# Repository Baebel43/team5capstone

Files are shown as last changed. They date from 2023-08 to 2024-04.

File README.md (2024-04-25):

# Ride Replay System 

## Executive Summary

Currently, there are no commercially available devices that officially allow people to ride a personal recording of a trail, Team 5 aims to change this with the Ride Replay Kit. The Ride Replay Kit aims to offer users the ability to replay a trail recorded anywhere with the same difficulty and immersion as if the rider was actually on that trail.

## Capabilities

The Project is able to do the following. For the indoor exercise bike, it is able to take a video and replay it on the trail with the ability to scale the video up and down based on the speed of the user. The Fan attached to the front of the indoor exercise bike will also scale with the user's speed. The outdoor bike that will have the ride replay kit attached is able to take in elevation data in after every full rotation of the back wheel. The full rotations are taken when the magnet attached to the spoke passes by the hall effect sensor attached to the back of the bike. This data is then saved to a text file and it can then be turned into a byte array for use inside the linear actuator code. The outdoor bike also has the ability to record audio from the microphone and store it on the Raspberry Pi. The Arduino IOT devices have the ability to communicate the weight input from the load cells and send them to the main controller Arduino IOT, these will be label so that future teams can know which is the slave and which is the master.

## Salient Outcomes

Being able to run the User Interface, the code to scale the video, the fan scale code, and the tachometer at the same time. Additionally the ability to use previous teams raspberry pi to record audio and a workmap accurately.

## Project Demonstration & Images

Minimally Functional Prototype link - https://youtu.be/p_Y5p9GWvbA

Ride Replay Kit - https://youtube.com/watch?v=LAPSdsN-WzQ&feature=shared

Final Trail Recording - https://www.youtube.com/shorts/GgyuamzpSRI

Exercise Bike Test - https://www.youtube.com/shorts/0spRPyzmJK8

## About Us

### Team 5
Team 5 is a six-person Fall 2023 to Spring 2024 Capstone Design team comprised of 5 Electrical Engineers and 1 Computer Engineers. The Team includes: Utsav Singa, Caleb Rozenboom, Jayden Marcom, Jesse Brewster, Caleb Turney, and Benjamin Ebel

#### Utsav Sigha
* Electrical Engineering Major
* Video System
* Video Software/Hardware

#### Caleb Rozenboom
* Electrical Engineering Major
* Resistance System
* Hardware

#### Jayden Marcom
* Electrical Engineering Major
* Work System
* Hardware

#### Jesse Brewster
* Electrical Engineering Major
* Audio System
* Audio Software/Hardware

#### Caleb Turney
* Electrical Engineering Major
* Immersion System
* Immersion Software and Hardware

#### Ben Ebel
* Computer Engineering Major
* GUI System
* Software/Coding in Python and C

### Faculty Supervisor

Professor Jesse Roberts of the Electrical and Computer Engineering Department of Tennessee Technological University.

### Stakeholders

The consumers of this project are mountain biking enthusiasts, exercise bicycle enthusiasts, and any person interested in an escape to a faraway place without the time or finances to do so. 

### Recognitions
* Jesse Roberts
* Conard Murray
* Jeff Randolph 
* Jeffrey Austen
* Sterling Sloan

## Repo Organization

This GitHub is comprised of 3 main files: Documentation, Reports, and Software.

### Reports

In the reports section of this repository information about the individual expectations for the reports and how they should be housed is provided.

### Documentation

In the documentation section information regarding the documentation that is required and how it should be organized is given.

### Software

In the software directory of the repo information regarding how each team is expected to document software can be found.

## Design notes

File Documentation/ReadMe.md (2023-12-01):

## Documentation Folder

This folder contains the folders for the signoffs, 3D models, Wiring Schematics, images, signoffs, and images for all of the subsystems

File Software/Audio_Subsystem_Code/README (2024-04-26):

This is the audio subsystem python code.

The Recording_microphone.py code is used to record the audio from the bike trail on the trail bike.
This code operates on the Raspberry Pi 3 within the Ride Replay kit. 
Run the code using a keyboard or SSH in to the Raspberry Pi.
The code will instantly start recording the audio from the microphone attached to the front of the bike. 
Then once the user has completed the trail. Jumper two pins 35 and 37 of the Raspberry Pi together and this will stop the recording. Alternatively, press "Enter" on the keyboard to stop.

The Audio_sectionalizing.py code is operated off of a separate computer. 
Place the name of the recorded trail audio file within the code and run.
An example code of the recorded trail audio file is "recorded_audio_2024-04-25_20-02-52.wav". Input this as the 'input_audio_file' varible on line 41 of the code.
This code divides the trail audio into 30 second sections, not matter the length of the video. The total number of audio files are outputted in the terminal. The audio files that are generated are label as "sectioned_audio_n" where 'n' is the number of the sectionalized audio file. 

The Playback.py code can be found on the Raspberry Pi 3 within the exercise bike. This code can be called within the main code 'RideReplayKitMainCode.py' where it runs. The 30-second sections of audio will play back based upon the feedback from the resistance system, where they will loop until the user has progressed to the next audio section. This syncs the audio with the user biking on the exercise bike.

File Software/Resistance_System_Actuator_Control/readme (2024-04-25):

This folder contains all the necessary code to run the linear actuator on the raspberry pi.

Once the workmap has been uploaded in a text file (WorkMapTest.txt), ActuatorControl.py pulls the file into an array which then is iterated through the equation in the Signoff.
To send the distance of the actuator (mm) to the actuator, it must be scaled by 0.1068 (Approximately. This value needs further calibration by testing each value with the actual distance.).

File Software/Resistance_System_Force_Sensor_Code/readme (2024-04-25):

This folder contains all code needed to allow the load cells to detect weight. 

Here is the link to the Amazon product where many helpful comments on setting up can be found:
https://www.amazon.com/DIYmalls-Weight-Digital-Amplifier-Arduino/dp/B09W2K13ZY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

For the HX711 board, here is the link for example code:
https://learn.sparkfun.com/tutorials/load-cell-amplifier-hx711-breakout-hookup-guide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

The Master.ino and Slave.ino code is for BLE transmission of the weight values (in lbs) from an Arduino IOT (slave) on the pedals and an Arduino IOT (master) which connects to the raspberry pi.

Helpful hints:
Make sure there is space below the load cells for the middle to bend. 
Keep the same calibration factor

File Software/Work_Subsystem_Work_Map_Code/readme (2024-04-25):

To set up the Work Map creation code you can find it in /scripts/testing/new as Work_Subsystem.py on the ride replay kit raspberry pi. You will need to power the Raspberry pi using a battery and start it either using an ssh or a hdmi plus keyboard. When you are finished jump the 35th pin to the 33rd pin and a workmap.txt will be created. The code will take pressure measurements every pass of the backwheel and will create an array using these values. These values can then be passed to the resistance subsystems code to be converted to height then to potential energy then to a workmap to be used by the resistance subsystem.

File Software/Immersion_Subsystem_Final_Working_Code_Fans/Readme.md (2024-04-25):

This is the code for the Atmega 2560 that is used to control the Fans.

This code controls both the PWM that drives the fan and the I2C connection the Raspberry Pi that allows that the Pi and Arduino to send data to each other. Make sure to consult the wiring schematic to ensure all the wires are connected to the correct ports or the code will not run properly. 

Also note that this code was created to run on the Arduino Atmega 2560. If you wish to run the code on a different Arduino, some of the registers and commands will need to be changed accordingly to match.

## Steps to Run Code:

1: Ensure that proper wiring has been done for the Arduino and Raspberry pi via the schematic. Ensure that the grounds of the external DC supply, Arduino, and Raspberry Pi are all connected. Ensure that the SCL and SDA pins on the Rpi are connected to the SCL and SDA pins on the Atmega. Ensure that the PWM wire of the fan is connected to Pin 9 on the Atmega.

2: Make sure that both the Arduino code and Raspberry Pi code are running simultaneously else there will be no connection and no data will be sent. Consult the Raspberry Pi software documentation for the necessary code to run.

3: Ensure that the power switch is set to on for the Immersion system enclosure, and that the fans are toggled on in the GUI. Failure to do so will result in the fans not running properly.

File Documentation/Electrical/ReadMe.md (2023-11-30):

This folder contains KiCad source files and PDFs for each of the subsystems.

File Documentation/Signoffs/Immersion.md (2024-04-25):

Team 5 - Ride Replay Kit

Team Members: Benjamin Ebel, Jayden Marcom, Jesse Brewster, Caleb Rozenboom, Utsav Singha, Caleb Turney

# Detail Design: Immersion System

##  Subsystem Functionality

The immersion subsystem will drive fans that are pointed toward the user. A tachometer on the bike wil be used to indicate how fast the user is virtually moving. Based on the speed measured, the fans will rotate at a specific RPM. The faster the measured speed, the faster the fans will rotate. The goal will be for the fans to simulate the speed of the wind outside by outputting at the same or scaled but similar wind speed. By having the fans adapt and change their speed based on the riders speed, a more immersive experience can be achieved, since the user will be able to artificially feel the changes in their speed.

Components from previous iterations of this project will be utilized for this subsystem. A tachometer was added to the bike by a previous team that was used as a speed sensor for the ride replay system. The previous speed sensor would take data from the bike as the user rode the trails, then that data would be sent through ble to a raspberry pi. The fans will be connected to this raspberry pi and the speed sensor data will used to either increase or decrease the rpm of the fans. Previous codes for the microcontroller will be utlized to allow ble communication and new code will be added to properly connect the fans to speed that is read. The previous power distribution system will also be used to power the fans. 

## Constraints 

|Constraint |Description |
|---|---|
|Off Switch| The Immersion system shall have an off switch implemented that allows the user to disable the system.|
|Fan Mapping| The fans will be mapped to output at a scaled version of outside wind speed |
|Fan Control| The speed of the fans will be adjustable and adaptable|
|Minimum RPM (DESCOPED)| The fan shall spin at a minimum of 1,105 RPM|
|Output Noise Level| The fans will have a max noise level output of 65 dBA|
|Power|Each of the fans will be supplied a minimum of 28.80 watts of power|

## Analysis

### Meeting the Fan Mapping Constraint

The speed from the previously installed speed sensor system will be used as the comparison data to decide on the fans speed. As the speed is read, the fans will change to rpm that is meant to simulate that speed. This Rpm will be based on many calculations that aim to match the outputted wind speed of the fans to the wind speed outside linearly.

Although the max speed one can achieve on a bike is above 100 mph, the average speed that a user will ride is anywhere between 10 for inexperienced riders up to 24 mph for more experienced riders [3]. This speed can reach upwards of 30 and 35 when the user is on an incline. With this in mind, the max wind speed of the fans will be connected to a max speed of 35 mph on the bike.

When it comes to choosing a fan for the immersion subsystem, it is important that the fan has a high enough CFM (Cubic Feet per Minute) value. CFM is the measurement of the volume of air that a fan is capable of moving. In order to convert CFM to a speed value you would have to know the measurements of the room and the static pressure within it. For the scope of this project, the goal is not to circulate air in the room but to push air from the fans on to the face of the user. It is impossible to precisely calculate the speed and the force that a fan will produce in an open space without being able to physically test it. So, for the sake of simplicity, a fan with a comparatively high CFM will be chosen and if the max power and speed ends up being too high then the maximum RPM of the fan will be limited. A PC cooling fan will have on average between 50-80 CFM depending on the quality and the size. This value needs to be marginally higher in order for the wind from the fans to reach the user and provide any sort of noticeable force. Therefore, the CFM-A225BF-158-597-22 has been chosen with a CFM value of 185.5 [2]. Extra testing will need to be done in regards to the distance of the positioning of the fans and their max power output, but this value should be adequate in pushing enough air towards the user to provide an immersive experience through changing speeds.

The goal of the immersion system is to have the speed of the wind that the fans output match the speed of wind outside while the user is traveling. Although there are many factors that can affect wind speed from a fan, for the sake of this project, it will be assumed that the air around the fan is perfectly stationary and all the air movement comes from the fans alone. It will also be assumed that the cross sectinal area that the flan is blowing into will be equal to the circumference of the fan. The diameter of entire CFM-A225BF-158-597-22 fan frame is 120mm, there is approximately 10 mm of frame so the diameter of the actual fan will be taken as 110 mm. This makes the radius equal to 55mm so if we find the cross sectional area, which is πr^2, then we get an area of 0.1023 square feet. The datasheets for fans do not include their winds speeds but instead their CFM so these values must be converted to get an idea of what the fans output wind speed will be. The formula to convert Cubic Feet per Minute to Feet per Minute is [9]:

**$$\ FPM = CFM/(Cross Sectional Area)$$**

Then by converting the Feet per minute to miles per hour, you get the wind speed in MPH.

If we take the max CFM value of the CFM-A225BF-158-597-22 fan, which is 185.5, then divide by the area of 0.1023 square feet and convert to mph, then we acquire an mph equivalent value of 20.6056 Mph. This will be used as the max value for the fan wind speed, and to connect it to the speed of the user the values will be scaled to match. This means that for the scope of this design, 20.6056 mph will be equal to 35 mph, which is the range of the outside wind speed values scaled down by 41.13%. With this scale factor in place, the cfm values for each mph in the range can be found, and then the appropriate rpm can be apllied.



Figure 1. Full Data set for MPH to RPM

As Shown in figure 1, the values from the speed range are scaled down to fit parameters, then using the CFM to MPH conversion formula that was previously outlined, the CFM at each of those scaled speed values is found. As will be explained more later, the CFM values for a fan and the RPM are directly proportional[8]. So by taking the max CFM value of 185.5 and the max RPM value of 5800 for the CFM-A225BF-158-597-22 fan, a ratio of 31.24 RPM to every CFM can be calculated. Using this, the relative RPM values for each of the calculated CFM values was found. 
For speeds of 1-6mph then value of the rpm of the fans will be set to the minimum value contraint of 1,105 rpm. This will be explained in detail further into the analysis but the purpose is to provide a minimum speed that will be required for air to reach the user.

These values match up to the desired range of wind speeds and relate to the speed of the outside wind linearly. In the code pwm code for the fans these values will be used as the basis for the speed of the fans, as the tachometer sends values the speed will be read, then the fan will change to the appropriate RPM value.

### Meeting the minimum RPM Constraint. (DESCOPED CONSTRAINT)

When calculating to rpms needed to create certain wind speeds with the fan, it is important to take into account how much air the fan will push, and if the amount of air will be sufficient when the fan runs at very low RPMS. The fans will be positioned apporiximately 1 meter away from the user, for the purpose of this project, we will assume that the minimum area that the fan will need to be able to blow air is a cubic meter. This translate to 35.3147 square feet of space. When it comes to CFM and RPM for fans, they are directly proportional[8]. This means for a 10% increase in rpm there will be an equivalent 10% increase in cfm. The max rpm of the CFM-A225BF-158-597-22 is 5800, and the max cfm is 185.5. This means that for every 1 CFM, there is an equivalent 31.266 RPM. If we take the 35.3147 Cubic feet value that was decided earlier, and translate that to an equivalent RPM value we get 35.3147 x 31.266 = 1,104.149 RPM. This is the hypothetical value based on calculations that the minimum fan speed needs to be to push air in a cubic meter of space, and this is ignoring any outside factors of static pressure or air flow. 

The minimum value that the fan will output is 1105 rpm, this will allow the user to feel the air even at the lower speeds where the calculated fan speed would initially not have been able to push enough air to reach the user. This is in line with the minimum constraint.
 
### Meeting the Fan Control Constraint

To create an immersive riding experience for the user, it is important that the fans are controllable and able to change their output based on the speed that the user is traveling. The CFM-A225BF-158-597-22 is PWM controllable meaning that it can be hooked up the PWM output of the Raspberry pi and its speed can be programmed using pulse width modulation. The speed of the user will be taken from the tachometer and sent to the Rpi and a code will be ran to use that speed data and convert it to a proportional output for the fan. As the speed data that is sent gets changed, a change in the speed of the fans will be noticeable as well. 

### Meeting Off Button Constraint

In the case that the user does not want to make use of the immersion subsystem, an off switch will be programmed into the fan code that will allow the user to shut the subsytem off. This will keep the fans from outputting until the user decides that they want to turn it back on. 

### Meeting Output Noise Level Constraint

While the OSHA standard limit for noise level is under 85 dB for 8 hours, that is not the only constraint that should be taken into account when using fans. For this susbsystem, the fans should be fast enough to properly provide air to the user, but not be so loud as to cause discomfort. Around 60 dB is the sound level of a normal conversation and past this noises start to be considered loud and potentially annoying. With this is mind, the constraint of 65 dB has been set for the fans maximum sound output. At this noise level, the fans will be very noticeable and easily heard but not at the level that should cause pain or discomfort to individuals.

According to the datasheet of the fan CFM-A225BF-158-597-22, it has a rated noise level 59.7 dBA. This value is less than 65 dBA meaning this fan will be sufficient in fulfilling this constraint.

### Meeting power constraint

<!-- In the previous renditions of this project, the groups created a power distribution system to power their componenets. The same method of powering will be used for the fans. The fans will be connected to the already installed raspberry pi which will deliver the necessary power. The raspberry pi being used is the Model 3 B+. The recommended amperage limit for the pi is 2.5 amps. The CFM-A225BF-158-597-22 is rated to operate at 5 VDC and an input current of 0.57 A. This equates to a total power draw of 2.85 Watts. The power distribution system is comprised of multiple DIN rail power supplies, each of which is capable of delivering 35 watts of power or more. Since two fans will be used for this subsystem, a total power of 6.648 W will be needed. This is within the capabilities of the previously built power system meaning the fans will be delivered their full power and be able to operate within their full range. -->

When it comes to the goal of this subsystem, it is important that the fans are powerful enough to push winds towards the user that provides ample force that is at least partially indicative of a physical trail riding experience. When considering the 5V fan options available on the market, they are not powerful enough or provide enough cfm to produce much wind force without being within a very close proximity to the user. With this in mind, 12V options had to be taken into account with the goal of a successful immersion system in mind. The Rpi is only capable of powering up to 5V fans, so an external power supply will need to be utilized in order to provide ample power to the fans and let them operate at their full range. The fans will be connected to the PWM GPIO of the raspberry pi and powered by an external source. 

The CFM-A225BF-158-597-22 fan is a 12V fan that is rated to have a current draw of 2.4 Amps equalling out to a power draw of 28.8 Watts. With there being two fans that means the total power draw will be 57.6 amps. With this in mind, a 12V 5A 60W power supply has been chosen to power the fans. It comes with a female DC connector piece that will allow a connection to fans. 

The CFM-A225BF-158-597-22 has 4 connections wires: +Vin, -Vin, and Tach signal, and PWM signal. The fan speed will be controlled via the PWM0 port GPIO12 on the raspberry pi. The fans will be connected to the external 60W power supply.

## Buildable Schematic



Figure 2. Circuit Schematic for Fan Connection to Raspberry pi

## Bill of Materials

|Item|Description|Part Number|Manufacturer|Quantity|Individual Price|Total|
|----|---|---|---|---|---|-----|
|Fan|DC Brushless Fan|CFM-A225BF-158-597-22|CUI Devices|2|$35.85|$71.7|
|PSU|DC 12V 5A 60W Power Supply||Arybroourd|1|$10.87|$10.87|
|Total|||Total Components|2|Total Cost|$82.57|

## References:

[1]“Decibels dBA,” Decibels dba, https://silentpc.com/articles/decibels (accessed Feb. 11, 2024). 

[2] “CFM-120BF series datasheet - axial fans - cui devices,” SERIES: CFM-120BF | DESCRIPTION: DC AXIAL FAN, https://www.cuidevices.com/product/resource/cfm-a225bf-153-577.pdf (accessed Feb. 12, 2024). 

[3] “Average cycling speed for new and experienced cyclists,” Road Bike, https://www.road-bike.co.uk/articles/average-speed.php (accessed Feb. 12, 2024). 

[4] T. N. Crouch, D. Burton, Z. A. LaBry, and K. B. Blair, “Riding against the wind: A review of Competition Cycling Aerodynamics - Sports Engineering,” SpringerLink, https://link.springer.com/article/10.1007/s12283-017-0234-1 (accessed Feb. 18, 2024). 

[5] J. Quinones, “4 ways to calculate wind load,” wikiHow, https://www.wikihow.com/Calculate-Wind-Load (accessed Feb. 18, 2024). 

[6] "DC 12 Volt 5 Amp Power Supply - 60W https://www.amazon.com/Supply-Adapter-100-235V-50-60Hz-Connector/dp/B0BJVVBBMJ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

[7] “Fan wind speed calculator,” Calculator Academy, https://calculator.academy/fan-wind-speed-calculator/ (accessed Feb. 22, 2024). 

[8] E. Gutowski, “The 3 fan laws and fan curve charts,” HVAC School, https://hvacrschool.com/the-3-fan-laws-and-fan-curve-charts/ (accessed Feb. 23, 2024). 

[9] M. A. Instructor, “Calculating CFM or velocity across a coil or in ductwork,” MEP Academy, https://mepacademy.com/calculating-cfm-or-velocity-across-a-coil-or-in-ductwork/# (accessed Feb. 23, 2024).

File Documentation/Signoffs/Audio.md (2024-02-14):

# Detail Design: Audio System
The audio subsystem records the audio from the bike trail and replays it on the exercise bike for the user to hear the environment of the trail.

##  Subsystem Functionality

The audio subsystem will use a unidirectional microphone mounted to the mountain bike to record audio from the trail. The audio will be recorded to a Raspberry Pi where a Python code will send it to a cloud based service where it will be processed to remove unwanted noises and improve audio quality through equalization and audio compression. The audio will also be divided into loop points depending on key points of interest throughout the trail. This processed audio will then go back on the Ride Replay Kit to the speakers of the exercise bike for playback while riding the trail. A separate Raspberry Pi will be responsible for the playback of the audio to the speakers. The audio should sync with the work map to give the user an accurate audio experience for when the user comes across different environments which produce different sounds. The speakers on the exercise bike will be mounted to the sides of the TV and allow the user to hear from both the left and right.

## Constraints 

|Constraint|Description|
|---|---|
|Recording audio without undesired noises|A unidirectional microphone will be used to reduce the pick up of audio from the bike and the user riding the bike. A wind mic filter will reduce wind noise.|
|Processing audio|The recorded audio will need to be stored and accurately played back for the user.|
|Syncing Audio with Work Map|Audio associated with specific distance must be synced with the correlated work value from the Work Subsystem.|
|Python Libraries used for audio processing and looping|The correct libraries must be implemented in order for the audio processing to occur in Python on a separate computer. The audio will need to loop upon key points of interest until the biker has reached the next section.|
|Limit Audio level output to speaker|Audio Output has to be limited to 80 decibels or less to reduce hearing fatigue. OSHA Law requires less than 85 decibels for 8 hours.|

## Analysis

### Meeting Noise Constraint

To record audio, a cardioid polar pattern microphone will be mounted to the front of the bike on a 12 inch arm to reduce the pick up of audio from the bike and the user riding the bike. The microphone will have a windshield on it to reduce wind noise. The Logitech Blue Snowball USB Microphone will be used for recording, and has the option to be switched from a cardioid polar pattern to an omni-directional pattern, meaning it can accept audio from all directions. Team 5 will only switch to use the omni-directional mode if the unidirectional cardiod pattern doesn't accurately record the environmental noises. This microphone is powered and transfers data through the USB 2.0 port on the Raspberry Pi 3 B. Once the audio is recorded on the mountain bike, the data on the SD card from the Raspberry Pi can be uploaded to the online cloud based service, Google Drive. Once the audio has been uploaded to the cloud, an external computer will complete the audio processing by using a Python code that Team 5 will be writing. An equalizer will be implemented that can apply a low-pass or high-pass filter to the audio to filter out any unwanted noises. For example, any hiss or squeaking from the bike is usually a high frequency noise and these can be filtered out with a low-pass filter applied to the audio. Any low frequency rumble or wind noises can be filtered out of the audio file through a high-pass filter as well. After the audio has been processed on the computer, the data will then be sent back to the cloud through which the Raspberry Pi on the exercise bike will run a Python code to transfer the audio back onto the exercise bike, through a separate Raspberry Pi 4.

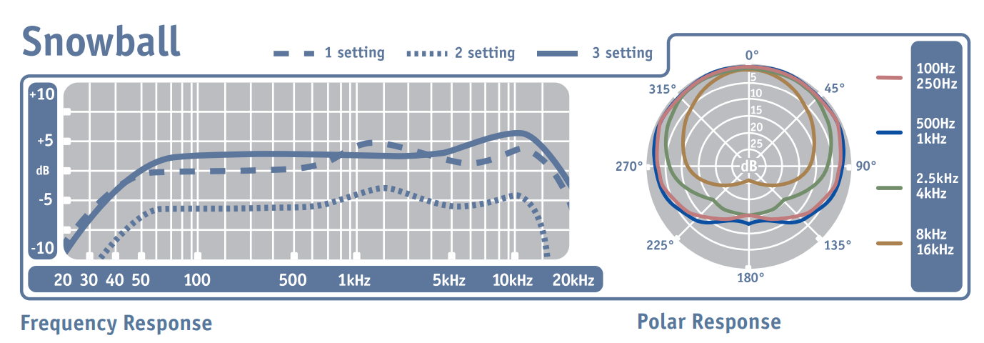
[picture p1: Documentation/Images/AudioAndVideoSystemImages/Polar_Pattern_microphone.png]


**Figure 1.** Cardioid and Omnidirectional Polar Patterns of Blue Snowball Microphone

### Meeting Processing Constraint

The audio recorded from the bike trail must be stored and accurately played back on the Exercise Bike. To ensure this is possible, the total data stored must be calculated.

Formula:

Bits per sample x samples per second = bits per second / 8 = Bytes per second x 60 seconds = Bytes per minute x 60 minutes = Bytes per hour.

Recording at: 16 bit, 44.1 KHz, Mono:

16 bits per sample x 44,100 samples per second = 705,600 bits per second. [88.2 KB per second] 
705,600 bits per second / 8 = 88,200 bytes per second x 60 seconds = 5,292,000 Bytes or 5.292 MB per minute. 
5.292 MB per minute x 60 minutes = 317.52 MB per hour.

Team 5 calculated that the maximum amount of ride time we recommend the user to ride is 4 hours. So with the microphone recording at 317.52 MB per hour x 4 hours = 1,270.08 MB or 1.2GB for 4 hours of recording. So the maximum audio file size recommended is around 1.2GB which falls within the 15 GB of space given by the Google Drive for free.

According to a benchmark taken of the Raspberry Pi 3, the SD card can be processed at 44.5 Mb/s meaning it would take approximately 28.5 seconds for the audio to process fully onto the SD card.

After the audio file has been recorded, it needs to be uploaded to the cloud through a Google Drive for processing on another, more powerful computer. To do this, the Raspberry Pi needs to be plugged into a computer and there will be a Python code that will transfer the data from the SD card and put it in the Google Drive. Within Python there is a library, pydrive, that allows the Raspberry Pi to upload audio files to the Google Drive, and this can be executed as soon as the Raspberry Pi is connected to the internet. 

### Meeting Syncing Constraint
The audio recorded from the mountain bike is to be synced with the distance and speed of the Work Map. However, an issue that could occur is, if during playback on the exercise bike, the user pedals at a slower rate than what was originally recorded, the audio may slow down and become pitched down as well. To prevent this from happening, the audio will be divided into sections and every time the user pedals slowly in that section, the audio will loop until they have reached the next section. The same concept will be applied if the user is pedaling faster than the original recorded speed. Once the user has finished the length of a section, quicker than normal, the audio will fade to the next section, thus syncing it with the work map.

Using this audio file, a spectrogram can be generated in Python to plot frequency over time. With this data, Team 5 can determine the points-of-interest throughout the duration of the audio recording. An example of these points-of-interest would be the sounds of waterfalls or terrain/environment changes. With the points of interest determined, the loop points can be more accurately determined. To create a smooth loop, the loop should occur during a consistently occurring frequency so it is less noticeable when the ending and starting of a loop occurs. For example, a point of interest would be passing by a waterfall and the loop should occur during this period and it should not loop back to before the waterfall because the audio in the loop would be noticeably different from the waterfall noise thus creating a choppy sounding loop.  

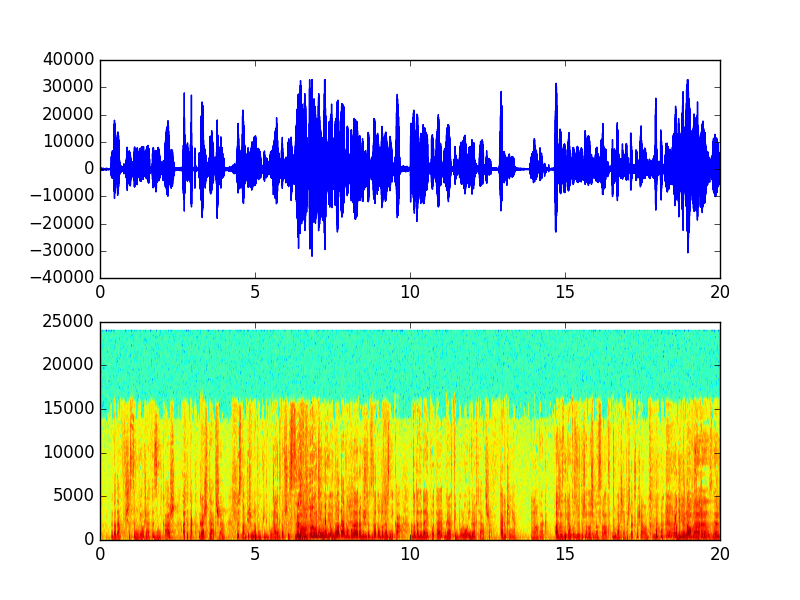
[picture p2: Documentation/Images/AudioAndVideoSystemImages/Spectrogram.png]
Spectrogram Example


**Figure 2.** Spectrogram Example Plot from Python

Above is an example of a Python generated Spectrogram using the 'scipy' library. Commonly occurring frequencies appear from 6 to 8 seconds into the audio clip. The time axis will be much larger but these are examples of good loop points that will be practically unnoticeable by the user.

The looping will have a crossfade applied to the audio loop to prevent sudden stopping in the audio to play back a previous section. This crossfading can be programmed to occur during playback when it takes an input and then determines which section of audio to playback. For transitions, the first audio clip will slowly decrease the volume as the next audio file slowly increases, until only the new audio section is playing. This should make for a more smooth transition to the looping of audio. 

In order to create this loop, the audio system will be linked to the work map to sync with the Visual and Resistance systems for an immersive experience. The Raspberry Pi accepts the time/speed that the user is at, and then once this data is obtained, it will move to the section of the audio file that the user should be in. The crossfade should occur during this transition period of one section to the other.

The audio recorded from the mountain bike is to be synced with the distance and speed of the Work Map. If the above solution does not work, an alternative solution is to divide the audio clip into 1 minute sections and every time the user pedals slowly in that section, the audio will loop until they have reached the next section. The looping will have a crossfade applied to the audio loop to prevent sudden stopping in the audio to play back a previous section.The same concept will be applied if the user is pedaling faster than the original recorded speed. Once the user has finished the length of a section, quicker than normal, the audio will fade to the next section, thus syncing it with the work map.

### Python Libraries used for audio processing and looping
The goal is to use Python to automate the processing for the audio to be sectioned into various loop points based on key points of interest that loop until the user proceeds to the next section. This is because Team 5 wants the capability to process up to a 4 hour recording. In order to create these loop points, the original audio file from the trail must be divided into many different audio files automatically through the use of Python and machine learning.

Within Python there are functions that can be used to apply a high-pass or low-pass filter to the two audio file formats, .wav and .mp3 files. There is also libraries and machine learning to create these loops based on clustering commonly occurring frequencies. These functions can be made with the following libraries: 
Pysqlite, numpy, librosa, scipy, pydub, pydrive, wave, math, matplotlib.pyplot., and scikit-learn

The 'pysqlite' library allows for interfacing with an SQL based Google Cloud service that the Raspberry Pi will upload the files to.

The 'numpy' library allows for recreation of the audio signal within python through processing arrays of data points. This allows for manipulation of the signal including filtering and other signal effects.

The 'librosa' library allows for analyzing and processing audio signals. This allows for importing of .mp3 files. This works along with the 'numpy' library and allows for manipulation of these .mp3 files. 'Librosa' also allows for the creation and computation of spectrograms of audio, which is a plot of audio frequency over the time of the audio clip.

The 'scipy' library is an extension of 'numpy' which provides additional capabilities such as signal processing. 

The ‘pydub’ library allows audio gain to be manipulated to match the 80 dB output described within the constraint section. It also allows for audio segmentation based on time, if necessary.

The ‘pydrive’ library allows for files to be uploaded to a Google Drive through python script. In this case, the Raspberry Pi will be uploading the audio file to the Drive through this library. 

The 'math' library allows for greater mathematical functions and number theory of the digital audio signal. 

The 'wave' library is included within the list, in case .wav files are needed instead of .mp3 files. This library allows for the reading of .wav files. 

The 'matplotlib' library allows for visualization of the audio file and spectrogram through plots.

The 'scikit' library is a machine learning library that will allow for clustering of audio that represent commonly occurring frequencies. From this, sectionalization of audio can be done and correct loop points can be established. 

The cutoff frequency of the audio file can be specified within the code depending on what the unwanted frequencies are. For example, a 50 hz high-pass filter may be applied to reduce rumble or wind noises.

### Meeting Audio Level Constraint

Team 5 will seek to create a volume limiter built into the audio playback system. This will limit the maximum amount of decibels to 80 decibels whenever the speaker is turned up to max volume. 

There will be a separate Raspberry Pi for playback of audio to the speakers. This Raspberry Pi has an 1/8" auxilary output that the Logitech speakers can plug into and output the processed audio.

Based upon the Sound Pressure Level (SPL Max) found on the Logitech Z207 specification sheet, the speaker can output an audio level of 88 dBA at 1 meter. The approximate distance from the speakers to above the bike seat, where the user riding the bike, is around 1 meter. This means the speaker is capable of outputing 88dB when the user is on the bike, thus the gain needs to be limited. This speaker volume can be adjusted through the audio processing on the Python code found within the library pydub. To prove this, Team 5 will create a SPL meter with a calibrated microphone to determine the speaker output gain at 1 meter from the speakers. Upon finding this gain, the loudness of the audio file can be adjusted so that when the speakers are turned all the way up to max volume the gain will be at or below 80 db.

Another issue that may occur, is if a gym worker or person is closer than the 1 meter length from the speakers, then the audio may be louder than 80 db to them. To solve this issue, a directional speaker cone can be 3D printed and mounted to each speaker to keep the sound projecting in the direction of the user only. This would mitigate the sound from getting to anyone standing beside the biker and keep the audio within the OSHA specification. 

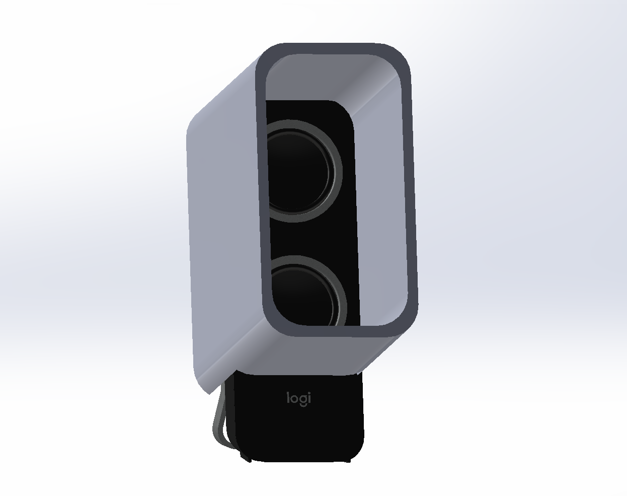
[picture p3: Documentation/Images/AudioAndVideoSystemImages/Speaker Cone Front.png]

**Figure 3.** Directional Speaker Cone

## Buildable Schematics

The schematic posted in GitHub represents an arm that will be mounted to the CAMVATE bike mount, which will mount the microphone 12 inches from the handlebars of the bike. An adapter will be needed to convert the cold shoe mount to a standard 5/8" camera thead, that the Blue Snowball Microphone has. This way the microphone will still be able to be mounted to the 12" arm, away from the user.

Shown in the buildable schematics below, the microphone will be mounted to the side of this 12 inch arm that also holds the GoPro camera using the cold-shoe mount. This arm will be mounted to the CAMVATE bike mount, which will mount the microphone and GoPro camera to the handlebars of the bike. This will ensure that the microphone does not pick up as much bike noise, user breathing noises, or any other extraneous noises. This is the ideal setup for picking up audio from the bike trail.

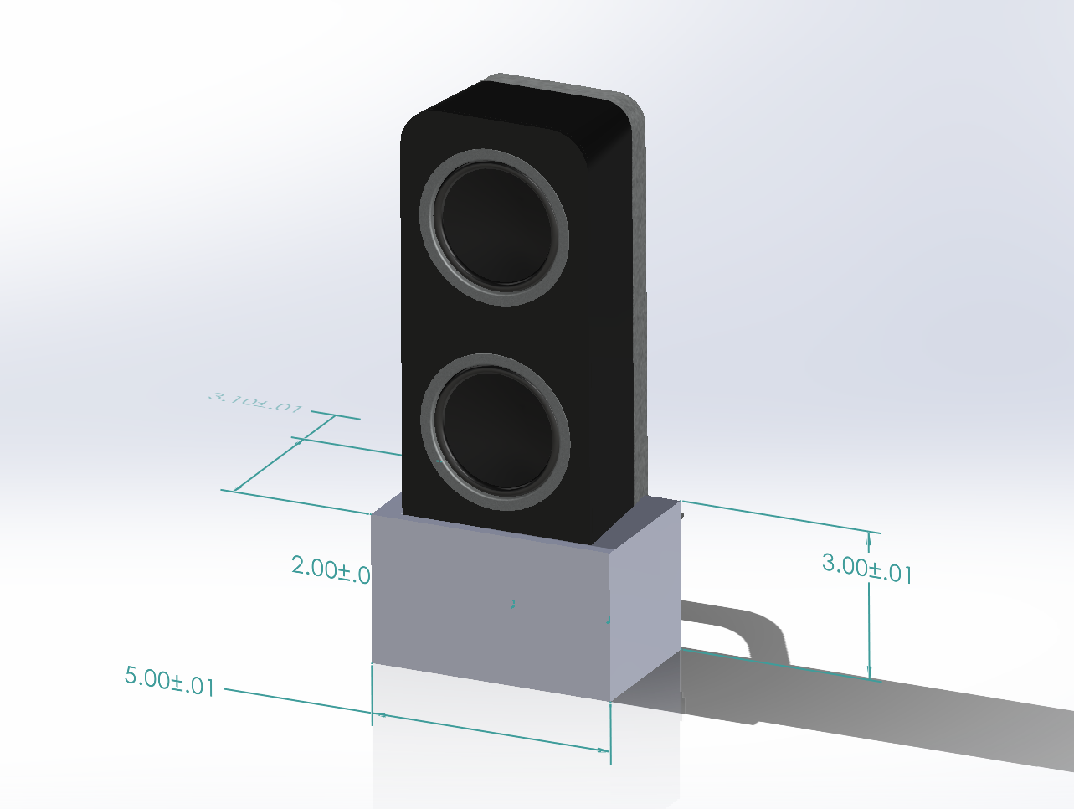
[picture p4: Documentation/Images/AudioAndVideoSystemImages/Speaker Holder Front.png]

**Figure 4.** Speaker Holder Front

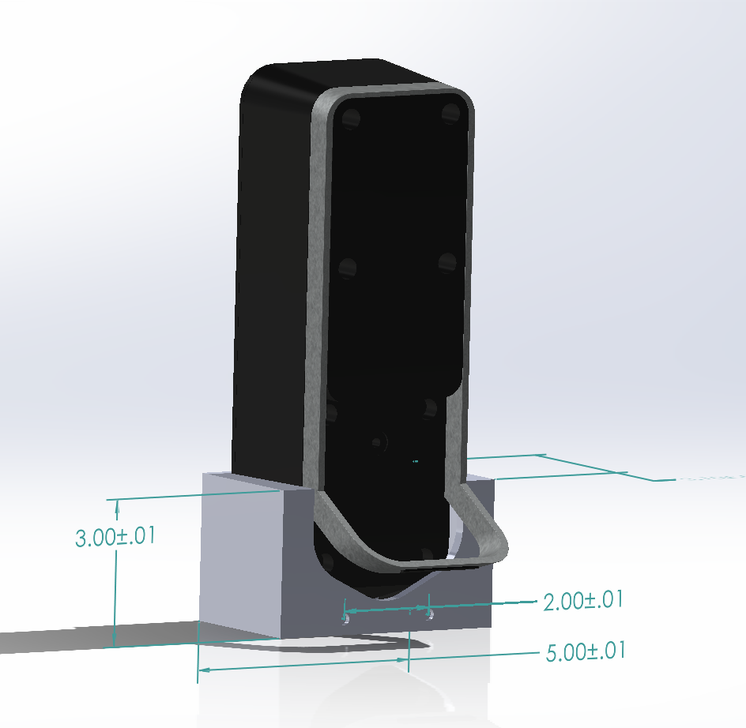
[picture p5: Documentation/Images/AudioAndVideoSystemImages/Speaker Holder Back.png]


**Figure 5.** Speaker Holder Back, With Screw Holes For Mounting

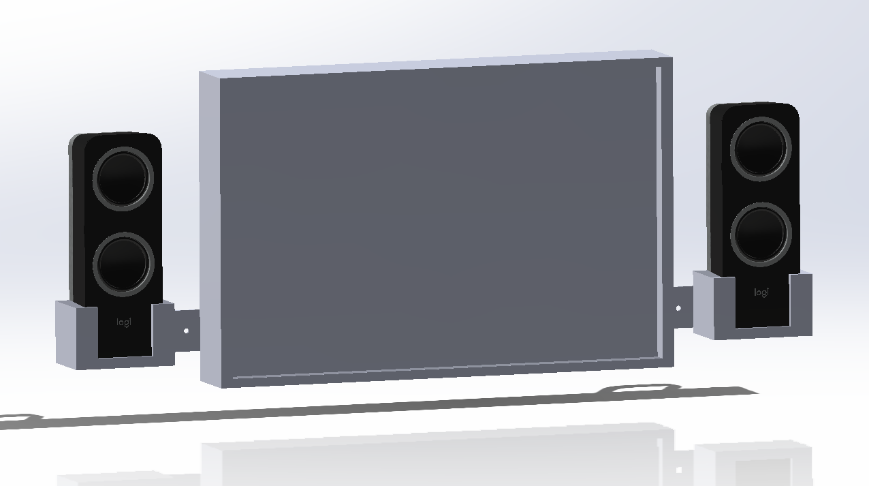
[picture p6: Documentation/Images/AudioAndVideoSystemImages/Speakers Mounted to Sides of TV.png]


**Figure 6.** Speakers Mounted to Sides of TV

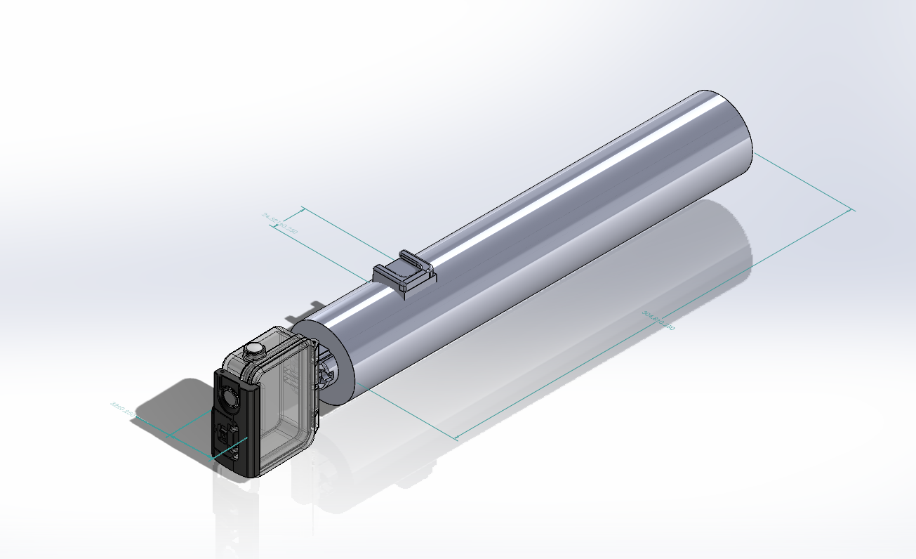
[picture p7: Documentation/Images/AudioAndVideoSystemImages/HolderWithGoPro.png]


**Figure 7.** Holder Side View With GoPro

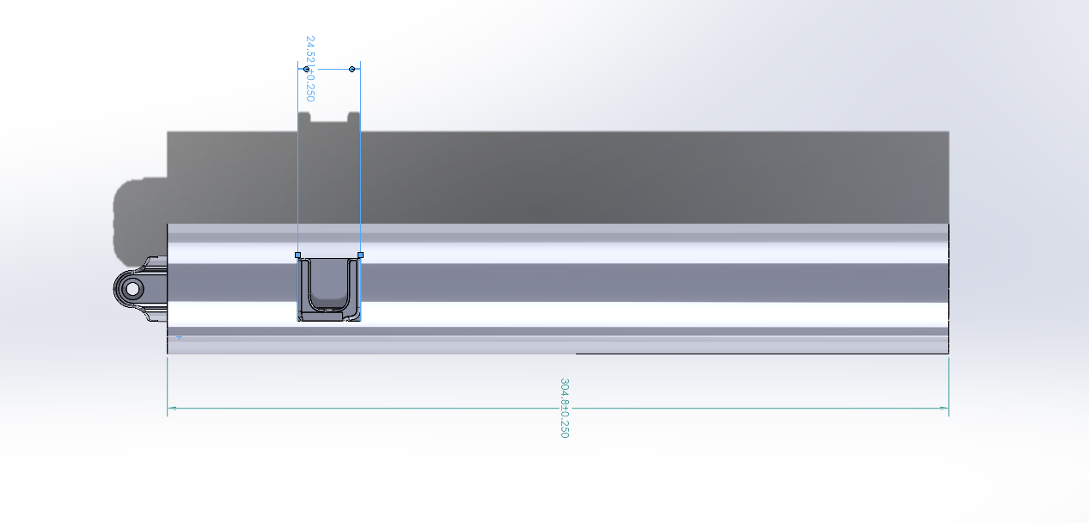
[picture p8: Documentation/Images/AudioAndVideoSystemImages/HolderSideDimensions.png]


**Figure 8.** Holder Side View Showing Microphone Attachment Dimensions

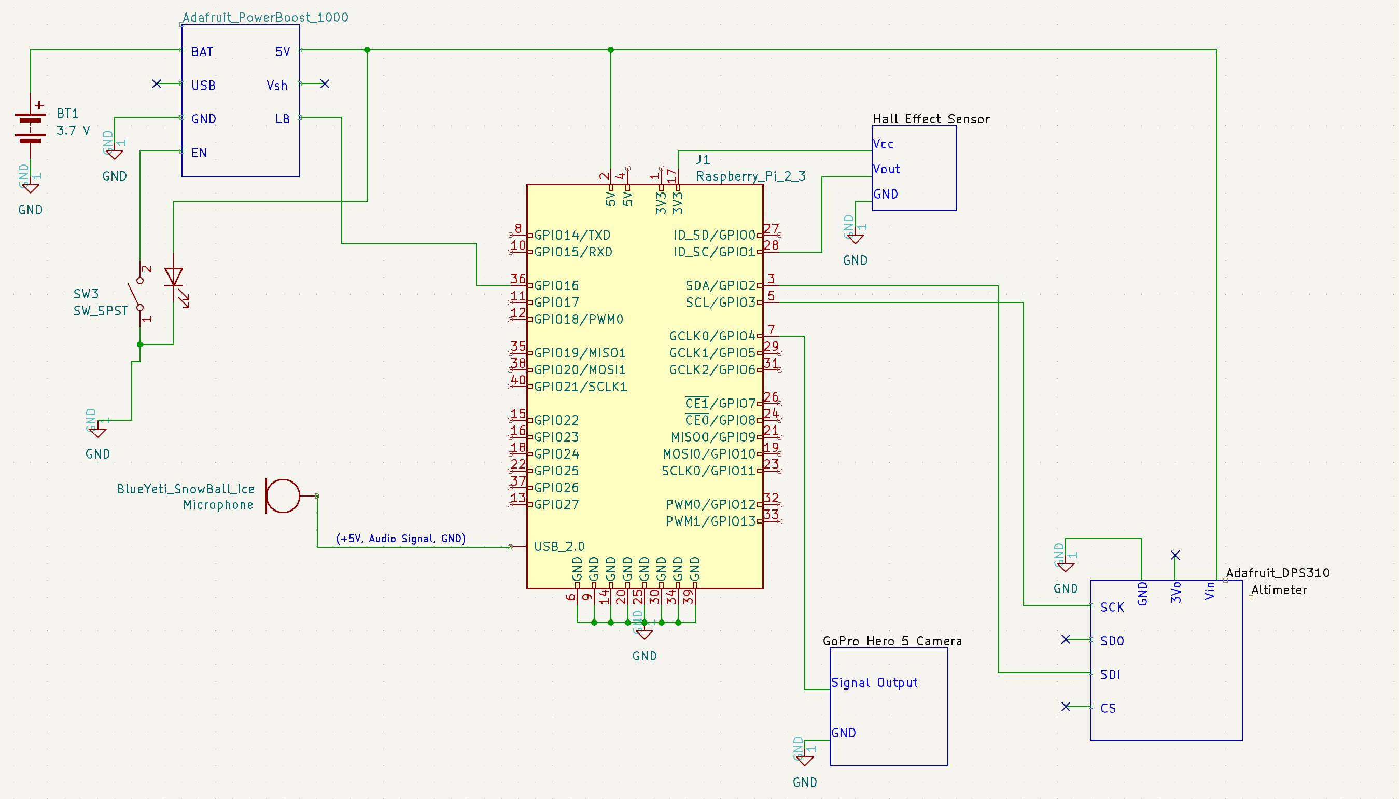
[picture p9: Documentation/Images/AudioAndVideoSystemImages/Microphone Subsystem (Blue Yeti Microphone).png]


**Figure 9.** Circuit Diagram for Microphone In Ride-Replay Kit

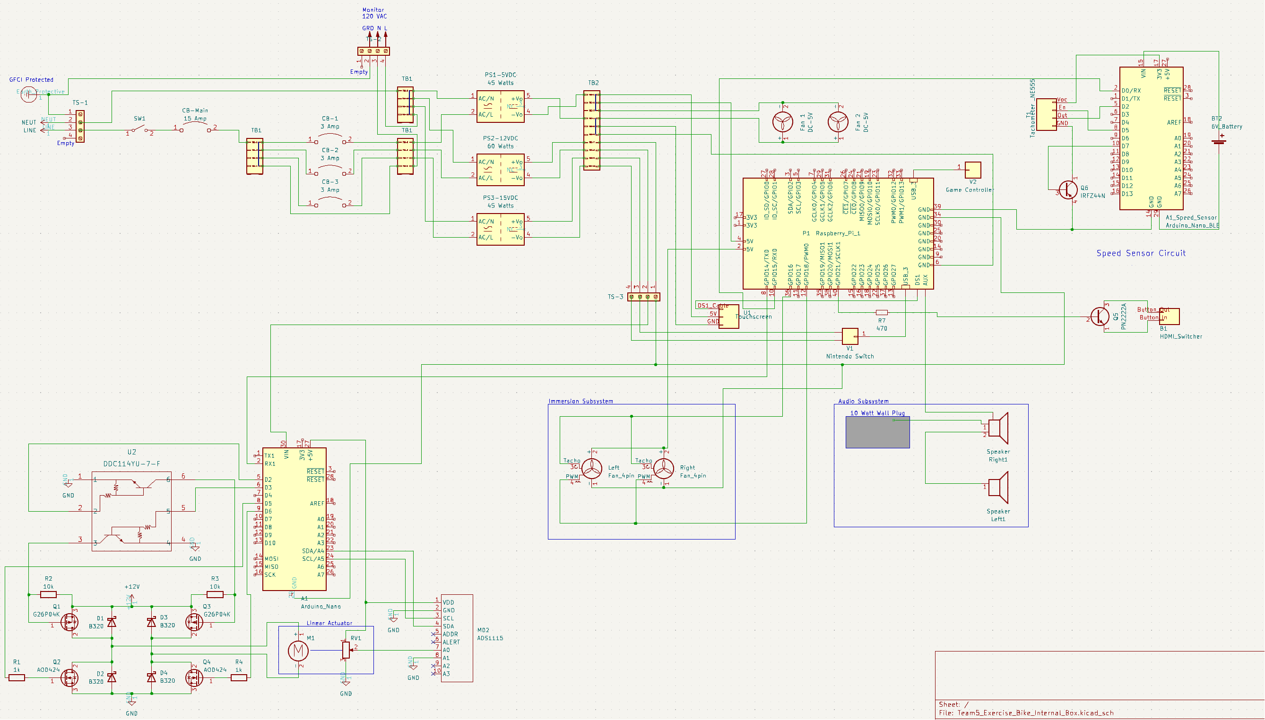
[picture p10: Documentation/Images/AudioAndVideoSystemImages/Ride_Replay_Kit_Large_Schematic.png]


**Figure 10.** Ride Replay Kit Schematic

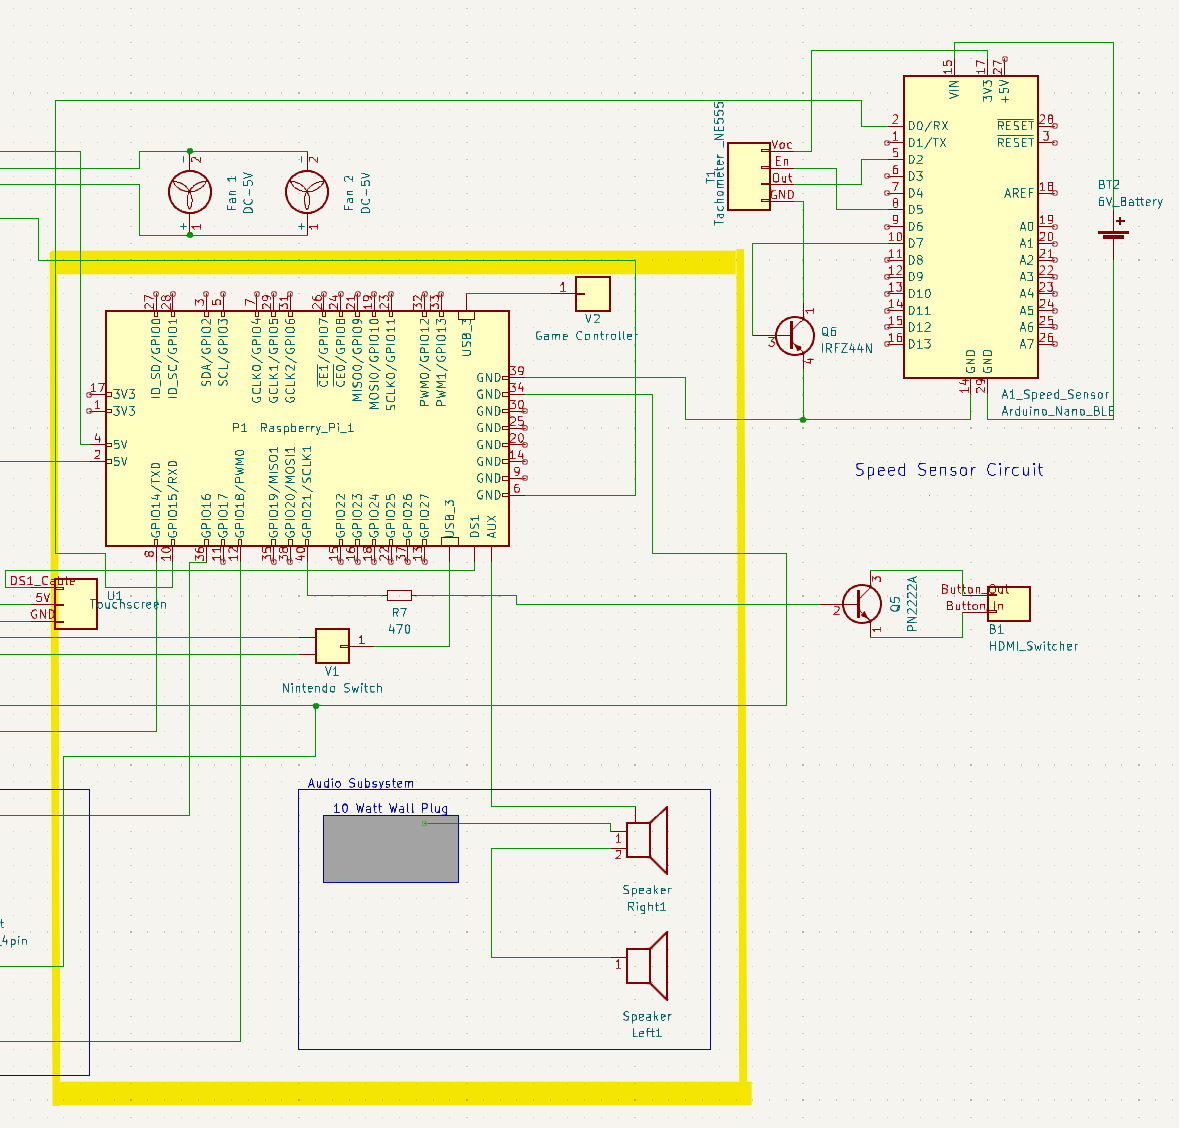
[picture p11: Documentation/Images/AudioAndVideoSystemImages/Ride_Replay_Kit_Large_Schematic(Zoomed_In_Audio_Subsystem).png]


**Figure 11.** Zoomed in Audio Subsystem Circuit Diagram

## Bill of Materials

|Item|Description|Part Number|Manufacturer|Quantity|Individual Price|Total|
|----|---|---|---|---|---|-----|
|http://tinyurl.com/yc6b6wyp|Logitech Blue Snowball USB Microphone for PC|988-000070|Logitech|1|$49.99|$49.99|
|http://tinyurl.com/6nshjt5v|Deadcat Windshield Wind Cover for Blue Snowball iCE|B07SF5C6BV|YOUSHARES|1|$9.99|$9.99|
|http://tinyurl.com/3r4b9tjt| 5/8"-27 Male Threaded Cold Shoe Adapter for Microphone Mount|0953|CAMVATE|1|$5.99|$5.99|
|http://tinyurl.com/yzzv7sss|CAMVATE Super Clamp with Cold Shoe Mount for Camera Flash Light|1814|CAMVATE|1|$15.00|$15.00|
|http://tinyurl.com/2xbv66vw|Logitech Z207 2.0 Multi Device Stereo Speaker|Z207|Logitech|1|$59.54|$59.54|
|http://tinyurl.com/2p9t866m|1-3/8 in. x 36 in. Zinc Steel Punched Flat Bar with 1/16 in. Thick|802037|Everbilt|1|$11.47|$11.47|
|http://tinyurl.com/mryprwj9|Universal Stainless Steel Vertical Pole Mount Adapterwith 3 Loops|Lighfast-SSJK-1P|Lighfast|1|$9.99|$9.99|
|http://tinyurl.com/2nu8f6ph|1/4-20 x 3/4" Button Head Socket Cap Bolts Screws, 304 Stainless Steel 18-8|AB10070201|EastLo|1|$7.99|$7.99|
||||||TOTAL|$169.96|

## References:

[1] Audio File Size Calculations
https://www.audiomountain.com/tech/audio-file-size.html
(accessed Nov. 1, 2023)

[2] microSD Card Benchmarks
https://www.pidramble.com/wiki/benchmarks/microsd-cards
(accessed Nov. 1, 2023)

[3] Scikit-Learn Machine Learning in Python] 
https://scikit-learn.org/stable/
(accessed Jan. 31, 2023)

[4] Volume Reducing Resistor in Speaker Lines
https://electronics.stackexchange.com/questions/278198/volume-reducing-resistor-in-speaker-lines
(accessed Jan 31, 2023)

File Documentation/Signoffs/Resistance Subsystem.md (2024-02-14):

Team 5 - Ride Replay Kit

Team Members: Benjamin Ebel, Jayden Marcom, Jesse Brewster, Caleb Rozenboom, Utsav Singha

# Detail Design: Resistance System
The resistance subsystem controls the linear actuator during a virtual trail. Team 5 will incorporate the previous iteration of this project's resistance system with the intent of changing the existing system into a user-interactive system. 

## Subsystem Functionality

The resistance subsystem has two main functions. First, the system must update the position on the work map generated by the work subsystem. This is done via two force sensors, one on each pedal. The force sensors will be sandwiched between two metal plates each (two on each pedal), providing equal force across the sensor. These two values will be averaged together and multiplied by the distance, which in this case, since the work map takes measurements every 2.1545 meters (the circumference of the bike tire), the distance will be 2.1545 meters. The averaged force value will be transmitted to the Raspberry Pi via Bluetooth, where the calculations will occur. Second, the system must change the linear actuator distance to match the current work value on the trail. This actuator distance will be calculated using the formula for the force between two magnets. This way, as the work done on the work map changes every 2.1545 meters, so the distance of the actuator will change to accomodate.

## Constraints 

|Constraint |Description |
|---|---|
|Work Recreation Accuracy | The work done on the trail must stay approximately comparable to the work done on the replay bike.|
|Magnet Distance Range | The distance range between the magnets and flywheel will be kept at 2-25 mm to keep the torque reasonable. |
|Force Minimum and Maximum | The minimum force value needs to be as low as possible to provide maximum sensitivity for the user. The maximum force value is set by the force sensor at 7000 lbs. |
|Housing Security | Resistance system must not fall of the pedal during operation.

## Analysis

### Meeting Work Recreation Accuracy Constraint

The most important part of this subsystem is the distance of the actuator to recreate the work done on the trail. This is calculated by rearranging the formula for the force between the two magnets. Although the flywheel is not technically a magnet, due to the eddy currents[1] created in the metal, it does create its own field and can be approximated as such. The change in work will be calculated by taking the first derivative of the work map. From there, the distance between the two magnets to create comparable work can be found.

The derivation starts with this formula[3]:

$$  F(x)=\frac{3\mu}{2\pi }M^{2}V^{2}\frac{1}{x^{4}} $$
- Where F is the force between the two magnets, µ is permeability of space (4πE−7 T·m/A), M is the magnetization, V is the volume (1.287E-5 m^3), and x is the distance between the two magnets.
  
The magnetization can be described as:

$$ M=\frac{m}{V} $$
- Where m is the magnetic dipole moment.

The magnetic dipole moment can be described as:

$$ m=\frac{BrV}{\mu} $$
- Where Br is the residual flux density, V is the volume, and µ is permeability of space. The residual flux density was calculated by the last team as 14,800 Gauss.

Rearranging the force equation:

$$ x=(\frac{3\mu}{2\pi }M^{2}V^{2}\frac{1}{F(x)})^{0.25} $$

- Since work is force times displacement, we can substitute F for W/d. D is the dispacement, which in this case is the circumference of the back tire. 

Final equation:

$$ x=(\frac{3\mu}{2\pi }M^{2}V^{2}\frac{d}{W})^{0.25} $$

Shown below are the Matlab graphs showing the previous calculations:

Matlab Graph

Figure 1. Matlab Graphs

Note: The derivative plot excludes negative values due to the actuator's incapacity to accept them. The actuator solely provides work and cannot receive it from the flywheel.

- The first graph is the work map as seen from the work subsystem. 
- The second graph is the first derivative of the work map so as to see the change in work. This graph has been shifted to the left so as to see where the next change in work will be wherever the work map position is. 
- The third graph is the distance between the flywheel and the magnet on the actuator. This was calculated using the formula derived above. 

Shown below is the Matlab code for the above graphs:

Matlab Code

Figure 2. Matlab Code

### Meeting Magnet Distance Range Constraint
  
This is an inhereted constraint to stay consistent with the original design[2] of the actuator. The range of 2-25 mm is mainly selected to not provide the user with too much or too little resistance. Team 5 will enforce this range via code in the Raspberry Pi. 

### Meeting Force Minimum and Maximum Constraint

The minimum force will be set as low as possible. According to the datasheet, the higher the feedback resistor, the more sensitive the force sensor will be (seen in Figure 1). Team 5 will calibrate the sensor to provide the most sensitive force possible. 

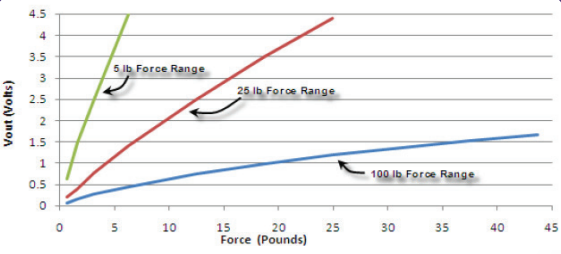
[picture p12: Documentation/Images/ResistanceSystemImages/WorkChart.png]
SolidWorks design of work system housing


Figure 3. Force Sensor Datasheet

### Meeting Housing Security Constraint
Velcro straps will be used to secure the resistance system force sensor circuit to the pedals. Four straps will be used, two on each side, to secure the force sensor that will be sandwiched between two metal plates. The metal plates will ensure equal force is distrubited to the sensor. See 3d models for more information. 

## Buildable Schematics

The housings for each of the two force sensor circuits will be placed below each pedal. The force sensors will be mounted to the top of each pedal, with wires running to the housings below. The bluetooth transmitter will then send the signal to the Raspberry Pi with the work map.



Figure 4. Design of Housing for Force Sensor Circuit



Figure 5. Design of Lid for Housing for Force Sensor Circuit



Figure 6. Force Sensor Housing on Pedal with Force Sensor and Plates(Velcro straps and wires not shown)



Figure 7. Side View of Above 



Figure 7. Force Sensor Circuit Schematic

## Bill of Materials

|Item|Description|Part Number|Manufacturer|Quantity|Individual Price|Total|
|----|---|---|---|---|---|-----|
|Force Sensor|Force Sensing Resistor Force Sensor 3175.15kgf (7000 lbs)|A401-25|Tekscan|3|$26.30|$78.90|
|Opamp|General Purpose Amplifier 4 Circuit Rail-to-Rail 14-PDIP|MCP6004-I/P|Microchip Technology|2|$0.59|$1.08|
|100 kΩ potentiometer|100 kOhms 0.5W, 1/2W PC Pins Through Hole Trimmer Potentiometer Cermet 1.0 Turn Top Adjustment|3386P-1-104LF|Bourns Inc.|1|$1.61|$1.61|
|Battery Holder|Battery Holder (Open) AA 3 Cell Wire Leads - 6" (152.4mm)|BC3AAW|MPD|1|$2.33|$2.33|
|47 pF capacitor|47 pF Mica Capacitor 500 V Radial|CD15ED470JO3|Cornell Dubilier Electronics (CDE)|1|$1.73|$1.73|
|Perfboard|Breadboard, General Purpose Plated Through Hole (PTH) Pad Per Hole (Round) 0.1" (2.54mm) Grid|ST-PERF-1-2|SchmalzTech, LLC|1|$1.95|$1.95|
|Arduino Nano 33 BLE|Arduino Nano 33 Bluetooth Low Energy Microcontroller|ABX00030 |Arduino|1|$26.30|$26.30|
|Total|||Total Components|10|Total Cost|$119.00|

## References:

[1]"Eddy Current Brakes for Haptic Interfaces: Design,
Identification, and Control,"https://ieeexplore.ieee.org/stamp/stamp.jsp?tp=&arnumber=4694782&tag=1

[2]”Spring2023-Mario-Kart-BikeV2 Resistance System,”
[Spring2023-Mario-Kart-BikeV2/Documentation/Signoffs/ResistanceSystem.md at main · TnTech-ECE/Spring2023-Mario-Kart-BikeV2 (github.com)](https://github.com/TnTech-ECE/Spring2023-Mario-Kart-BikeV2/blob/main/Documentation/Signoffs/ResistanceSystem.md)https://github.com/TnTech-ECE/Spring2023-Mario-Kart-BikeV2/blob/main/Documentation/Signoffs/ResistanceSystem.md

[3]"Force between two cylindrical magnets,"https://en.wikipedia.org/wiki/Force_between_magnets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,magnet%20and%20the%20dipoles%20of%20the%20second%20magnet.

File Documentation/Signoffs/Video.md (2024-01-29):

Team 5 - Ride Replay Kit

Team Members: Benjamin Ebel, Jayden Marcom, Jesse Brewster, Caleb Rozenboom, Utsav Singha

# Detail Design: Visual System

##  Subsystem Functionality

The visual subsystem uses the user’s current distance traveled on the recorded trail, and displays the frame from that point to the user on the screen. The video will replay back to the user at minimum 60 FPS at 1080p resolution. In the case that the user is replaying the trail slowly, the Ride Replay kit will utilize frame interpolation to maintain the smooth visuals, to avoid choppy video replay. 

## Constraints 

|Constraint|Description|
|---|---|
|Minimum Recording FPS|Video must be recorded at or above 60 FPS to ensure smooth video output to the user even at low speeds|
|Minimum Resolution|Video must be recorded at and display at or above 1080p|
|Minimum User Speed|The replay must support the user going minimum 25% of the recorded speed with smooth video|
|Storage Space Requirements|Replay video must fit on 2TB micro SD Card|

## Analysis

### Meeting Frames Per Second Constraint

Experts say the human eye can only perceive up to 60hz-75hz [1]. The GoPro Hero 5 can record video at 30FPS to 120FPS. Team 5 will record trails at 120FPS to not only minimize the amount of frames needed from frame interpolation, but also cause smoother video for the user when replaying the trails at low speeds. The HDMI splitter inherited from the previous teams limits FPS outputs to 60 FPS. Because of this limitation, the output from the system can only be at 60 FPS. This also ensures that the user will have smooth video as it stays within the 60-75hz range.

### Meeting Resolution Constraint

The GoPro Hero 5 can record from 480p to 4K. The max resolution that can be recorded while maintaining 120FPS is 1080p, which is also the resolution limitation for the HDMI splitter from the previous team. The goal of the visual subsystem is to be immersive, which includes picture resolution, so to make the experience as immersive as possible, the max resolution capable should be used, which is 1080p. 	

### Minimum percentage of recorded speed

The recording will be done at 120 FPS, and the resulting video will be put into frame interpolation software to create inbetween frames resulting in 240 FPS. The inherited HDMI splitter only has capabilities up to 1080p 60Hz, which limits video outputs to 60 FPS. Now using the interpolated video of 240 FPS, the video can support users going 25% of the original trail’s speed, while maintaining smooth visuals.

$$ \frac {\text {Limitations Of Monitor}} {\text {Interpolated Video FPS}} * 100 = \text {Minimum Percentage of Recorded Speed} $$

$$ \frac {60 \text {FPS}} {240 \text {FPS}} * 100 = 25 \verb|%| $$

Team 5 will not interpolate the video more than once as to not take up too much storage space.

### Meeting minimum storage requirements

With the goal of 4 hours of video, the calculation for the storage space needed for each recorded ride is as follows:

$$ \frac {\text {Bitrate}} {8} * \text {Time (In Seconds)} = \text {Video Size} $$

$$ \frac {60 \text {Mbps}} {8} * 60 \text{seconds} * 60 \text {minutes} * 4 \text {hours} = 108\text{GB} $$

These calculations already take the GoPro Hero 5’s video compression into account.[2] Also, with the interpolation scaling the video to 240FPS, the video will now take 216GB of space. With this calculated, the SD card can now fit up to video files.

### Syncing with Work Subsystem
	
The video output from the Visual Subsystem needs to synchronize with the Work Subsystem. This is to ensure the user’s visuals are in sync with the current point in the work map they are experiencing. For instance, if the video shows the user going up a hill, they will also experience increased resistance due to the work map. This will be done by associating each frame recorded or interpolated with a specific distance, and then display each frame depending on the distance the user has traveled in total. This constraint is essential to make the replays immersisive to the user.

### Obtaining Interpolated Frames

As mentioned before, the FPS of the recorded video will need to be doubled, to ensure that the user has smooth video replay when progressing slower than then original recording. Team 5 will be using the free AI frame interpolating tool called Flowframes Video Interpolator to interpolate the recorded video. Team 5 then move the interpolated video onto the RaspberryPi to replay to the user.

### Scaling Video Replay

Team 5 will know the distance the user has traveled every second and from this can calculate the speed the user is going at that given time on recording bike. Using the previous team's tachometer, Team 5 can calculate the revolutions per second to get the speed the user is going and the distance the user has traveled on the excercise bike. Using these two speed values, ratio can be made to match the excercise bike's video to the replay of the trail, with the ability to scale the video. All of these calculations can be done with Python code, and the video speed scaling can be done through Windows Media Player as it has the ability to accept Python scripts. Windows Media Player will be used as the playback method as it can display video.

## Buildable Schematics

Holder Side With Gopro
Figure 1. Holder With GoPro Side View

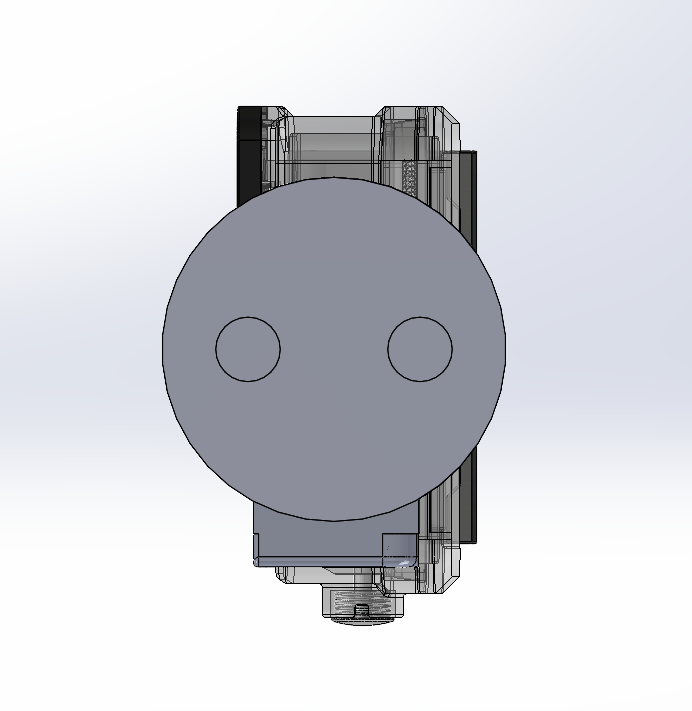
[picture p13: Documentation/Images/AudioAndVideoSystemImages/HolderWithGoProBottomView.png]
Holder Bottom With Gopro

Figure 2. Holder With GoPro Bottom View

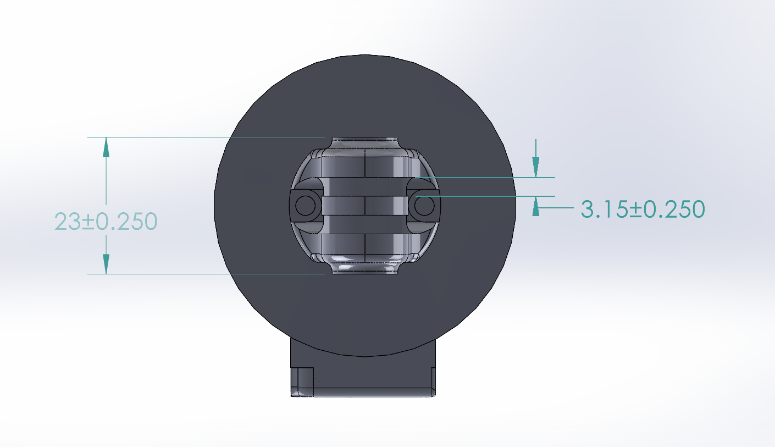
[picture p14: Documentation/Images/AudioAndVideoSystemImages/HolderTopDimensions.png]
Holder Top Dimensions

Figure 3. GoPro Attachment Part Dimensions

Holder Side Dimensions
Figure 3. Dimensions for Microphone Attachment

This electrical system is fully contained within the GoPro, so there is no electrical schematic for this system.

## Bill of Materials

Item
|Description|Part Number|Manufacturer|Quantity|Individual Price|Total|
|---|---|---|---|---|-----|
|GoPro Hero5 Black|Waterproof Digital Action Camera for Travel with Touch Screen 4K HD Video 12MP Photos|CHDHX-502|GoPro|1|$374.52|$374.52
|Total||||Total Components|1|Total Cost|

## References:

[1] V. Sierra, How Many Frames Per Second Can We Actually See In?, Arizona Retina Project, Available: https://azretina.sites.arizona.edu/node/837 (accessed Oct. 30th, 2023)

[2] C. David, GoPro HERO5 Black Video Sizes, Framerates, Modes & Options, Have Camera Will Travel, Available: https://havecamerawilltravel.com/gopro/video-hero5-black/ (accessed Oct. 30th, 2023)

[3] “Hero 5 Black User Manual” https://gopro.com/content/dam/help/hero5-black/manuals/HERO5Black_UM_ENG_REVD_Web.pdf (accessed Oct. 30th, 2023)

[4] "Flowframes - Windows GUI for Video Interpolation" "https://github.com/n00mkrad/flowframes"

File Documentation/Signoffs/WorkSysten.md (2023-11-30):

Team 5 - Ride Replay Kit

Team Members: Benjamin Ebel, Jayden Marcom, Jesse Brewster, Caleb Rozenboom, Utsav Singha

# Detail Design: Work System

##  Subsystem Functionality

The work subsystem uses the weight of the user, the velocity of the bike, and the elevation of the trail in order to create a work map for that trail to be replayed on the exercise bike. This work map will be altered based on the difficulty level the user selects in the user interface subsystem. A Hall effect sensor will be used to count the number of revolutions of the wheel to calculate the distance for use in the total work calculation of the trail. An altitude sensor will be used to detect the change in height throughout the trail and is used in the work calculation. The weight of the user will be converted to kg to be used in the work calculation. 

## Constraints 

|Constraint |Description |
|---|---|
|Distance between the box attached to the bike frame and the spoke|The measured minimum distance between the bike spoke and frame was found to be 30 mm meaning that the device can be no larger than 20 mm in depth protruding from the frame in between the spoke and the frame.|
|Magnetic Sensor Range|The magnetic sensor can be no more than 23.75 mm away from the magnet and it can be no closer than 12.7 mm.|
|Diameter of the Wheel|The device must support the minimum wheel size of 45.72 cm in diameter.|
|Sensing Speed (Minimum and Maximum Velocity)|The maximum velocity the sensor will be able to detect is 190 miles per hour. The Minimum velocity supported is 0 miles per hour.|
|Splash Resistant|The kit shall have the ability to withstand splashes from puddles and rain.|
|Ride Time|The user will be able to use the kit concurrently for 24 consecutive hours.|

##Analysis

### Meeting distance constraint

The average distance between the frame and the spoke of a mountain bike is between 30 mm and 35 mm. So to account for a 0.5-inch wiggle of the back wheel the maximum distance the box enclosing the device can protrude from the side of the frame to the spoke is 20 mm.

### Meeting Magnetic Sensor Range Constraint

The Hall effect sensor has a voltage draw of 3.3 V to 5 V that produces a magnetic flux density of 39 mT, equivalent to 390 Gauss [1]. Based on these specifications there must be a magnet opposite of the sensor capable of producing a magnetic flux density of at least 390 Gauss to trigger the sensor. By using a 1 ¼” diameter by ¼” thickness nickel-based magnet it will produce 456 Gauss at a distance of 22 mm. The distance of 22 mm is found to be the largest possible distance between the magnet and the sensor. The space between the bike spoke and the frame is 30 mm, minus the thickness of the magnet (6.35 mm) and the thickness of the sensor (2.06 mm) which equals 21.59 mm which is then rounded to 22 mm to ensure that it will reach a slightly above 21 mm.

- The residual induction for the magnet chosen is 14,800 gauss. The thickness of the magnet is 0.25 inches or 6.35 millimeters. The radius of the magnet is 0.625 inches or 15.875 millimeters. The maximum distance from the magnet and sensor we calculated was rounded to 22 mm. Using the following formulas we can solve for gauss at maximum distance to prove that it is above the 390 gauss required by the sensor.
**1 Tesla = 10,000 Gauss**

$$ B = \frac{B_r}{2} * ( \frac{D+z}{\sqrt{R^2+(D+z)^2}} - \frac{z}{\sqrt{D^2+z^2}} ) \text[2] $$

- Plugging in all the values: Br is 14800, D is 6.35, R is 15.875, and z is 22 mm we get  455.8 gauss which is well above the required value for the sensor.

The Hall effect sensor has a quiescent voltage between 0.535 V and 0.665 V [1]. This is used for the range of the linear output voltage which has a minimum of the quiescent voltage and a maximum of the voltage delivered to the device (3.3 V or 5 V) minus 0.2 V [1]. Using an Arduino Nano 33 BLE we can set the voltage threshold to the driving voltage of the Hall effect sensor minus 0.2 V to be a 1 and anything below this value to be a 0.

### Meeting the Diameter of Wheel Constraint

The minimum wheel size has been set at 18 inches to account for the average wheel size of the smallest type of bike that would be commonly ridden on a trail, a BMX bike [3]. The largest wheel size has been set at 32 inches which is 3 inches above the most common largest mountain bike tire at 29 inches [4]. Additionally, this constraint for minimum wheel size is set to ensure that the device should not be fully submerged in water. If the rider were to hit a 9-inch deep puddle it would most likely not only result in the destruction of the device but also a failure of the bicycle.

- This is proven within the calculations for velocity

### Meeting the Sensing Speed Constraint

The Maximum Velocity that the Work System supports should be no higher than 190 miles per hour to account for the fastest speed achieved on a bike being 186 miles per hour [5]. The minimum speed that needs to be supported is 0 miles per hour. This will allow users to reach very small speeds without having to worry that the Kit will not record the data to the Work System. 
The Maximum Velocity that the Work System can record at is well above the 84.94 m/s or 190 MPH value set by the constraint. The minimum velocity that the kit can support is no velocity at all and can support extremely small changes in velocity as long as the interval between rotations does not exceed the battery life of the system.

The minimum diameter that needs to be supported is 18 Inches based on the justification of a system and bike failure in the meeting the diameter of the wheel section. To ensure our system will still support 190 mph without having a sensing error the following calculations must be done:

Since the Hall effect sensor selected allows for measurements not only in front of the magnet but offset as long as the magnet is facing the correct direction. The magnet will be fixed in position which means that the sensor will begin to pick up the magnet before the magnet is directly in front of the sensor. To figure out what the furthest distance the magnet can be before the sensor begins or stops picking up the magnet, the formula used within the Meeting the Magnet Constraint section can be employed. Using the formula again and instead of calculating for Gauss which is given as 390 we calculate for distance. Solving for distance the value 23.85 mm is calculated this can be proved by plugging all the values as before replacing 22 mm with 23.85 mm (This will provide a gauss of 390.007).  Given the two values which are 22 mm which is maximum distance when the magnet is directly in front of the sensor and 23.85 mm which is the maximum distance the magnet can be from the sensor such that the sensor will detect it. The distance on the circumference of the circle that the magnet can be on can be calculated. First take 22 mm which is one leg of a triangle and take 23.85 be the hypotenuse we can calculate the other leg of the triangle is 9.2 mm. This is half of the value that is the straight line distance that the magnet can be along the circumference since the sensor is placed on the circumference it extends both ways making the actual measurement 9.2 mm both ways or 18.4 mm total. 

Once the arc length is solved then take the arc length and divide it by the total circumference to get the percentage of time spent within that arc length. The fastest value the system will support is 190 mph or 84.94 m/s. Using this value and the value for circumference we can calculate the total time for a rotation. Then take the percentage and solve for time spent within  the arc length calculated before.

Circumference for a 18 inch wheel in meters is 1.44 meters. Radius in meters for an 18 inch wheel is 0.2286 meters. As found before the distance between two points on the circumference is 9.2 mm. Max Speed is 84.94 m/s. Using these values the following can be calculated

**Total Time for Rotation = $$\ \frac{1.44 \text{ meters}} {84.94 \text{ (meters/second)}} = 16.9 \text{ Milliseconds} \text{   (Time)}$$**

**Angle Between the two Points = $$\ 2 * \arcsin{(\frac{(\frac{(9.2*10\^{-3} \text{ meters} )} {2})} {0.2286 \text{ meters}})} = 2.306 ^{\circ}  \text{  (Angle of an isosceles triangle)} $$**

**Half the Total Arc Length = $$\\frac {(1.44 \text{ meters} * 2.306^{\circ} )} {(360^{\circ} )}= 0.009224 \text{ meters} \text{  (Arc Length)}$$**

**percentage of arc length of the circumference = $$\ \frac{0.009224 \text{ meters}}  {1.44 \text{ meters}} * 100 \verb|%| = 0.6406 \verb|%| \text{  (Percentage Calculation)
}$$**

**Total Time Spent in Half the Total Arc Length = $$\ 0.6406 \verb|%| * 16.9 \text{ Milliseconds} = 0.1083 \text{ Milliseconds} \text{  (Time Spent within the Percentage)}$$** 

As mentioned before this measurement is only the measurement in one direction, to get the actual time spent in the total arc length multiply the total time spent in half the total arc length by 2. This results in 0.2165 Milliseconds spent in the total arc length. The measuring frequency of the hall effect sensor chosen is 20 KHz. Plugging these values the amount of times that the sensor will read the magnetic gauss value is determined.

**$$\ \frac{1}  {20\text{kHz}} = 0.00005 \text{ seconds} \text{   (Seconds from Frequency)}$$**

**$$\ \frac{0.2165 * 10\^{-3}\text{ seconds}} {0.00005 \text{ seconds}} = 4.33 \text{  (Total amount of times the value is read)}$$** 

This means that the sensor will read the gauss value 4 times at 190 mph at 18 Inches diameter.  As long as the velocity doesn’t increase and diameter smaller or larger than this will have relatively the same value of reads.

The sampling rate for the Arduino chosen is 16 ksps. Doing the same calculation as before we can solve for the amount of times the Arduino will read the measurements from the hall effect sensor during the Total time Spent in Total Arc Length that was calculated before at 0.2165 Milliseconds.

**$$\ \frac{1}  { 16 \text{ksps}} = 0.0000625 \text{ seconds} \text{   (Seconds from sampling rate)}$$**

**$$\ \frac{0.2165 * 10\^{-3}\text{ seconds}} {0.0000625 \text{ seconds}} = 3.464 \text{  (Total amount of times the value is read)}$$** 

This means that the Arduino at the sampling rate will measure 3 times during the period that the sensor will be in the required gauss zone.

### Meeting the Splash Resistant Constraint

A box shall house the work system. The components inside the bike along with the box will be coated in a splash-resistant silicone to prevent water damage from occurring. This is in the case that the rider is to use the Ride Replay Kit in the rain or ride through a body of water that could potentially splash the work system or fully submerge it. The electronics will be coated in an acrylic conformal coating that will be done using a 419D Liquid that protects from moisture and is certified IPC-CC-830B [6]. To seal the box to add a second layer of protection an acrylic-based sealant will be used and conforms to the military specification MIL-46106 which provides a strong sealant and water repellent.

### Meeting the Ride Time Constraint

Since there are many different trail lengths and skill levels, there is no set amount of duration for trails. Due to this, the minimum amount of time that the batteries should last is hard to make a specific number for. Team 5 decided to set the minimum amount of time at 24 hours. This allows users to record large trails without having to worry about the batteries not lasting the entire trail. Team 5 has chosen three AA Lithium Iron Disulfide batteries (Energizer Lithium Batteries)  in series to produce a voltage output of 4.5V for around 3000 mAh at 0 degrees Celcius [7]. These batteries were chosen based on the decay rate of the batteries at a load of 250mA and 100mA. At 250mA draw between 1.4V and 1.6V, the batteries will last for 14 hours. At 100mA draw between 1.4V and 1.6V, the batteries will last for 35 hours. Since our device will draw 25 mA we have more than met this constraint. 

- To solve for the maximum time the battery can last, the amperage output for each device and the milliamp hours output of the batteries are needed. The following values are needed: the current draw for the I/) of the Arduino Nano 33 BLE, the current draw for the Hall effect sensor, and the current output of the battery. The values are 15 mA from the Arduino I/O and 10 mA from the Hall effect sensor. The following formulas can be used:

  **$$\ \text{Amphours} = \text{Amps} * \text{Hour}$$**
  
  **$$\ \text{Hours} = \frac{\text{Amp Hours}}  {\text{Amps}} $$**
  
- Using these equations we can solve for the hours the device will last with brand new Lithium Iron Disulfide batteries. At around 3000 mA hrs divided by 25 mA, the device should last 120 hours under ideal conditions.

Based on the graph of continuous discharge at 250mA at 0 degrees Celsius the battery does not start to drop to a voltage that would not power our device at a draw of 3.7V until 10 to 11 hours of use and then completely stops providing a voltage at 14 hours. So the battery truly only gets a 5/7 of its lifespan for our device at the voltage needed. This means that at 25 mA under the same conditions would only provide around 120 * 5/7 = 85 hours of use [7]. 

### Creating a Work Map

- Creating the work map is the overall goal of the Work System. To do this altitude change, distance, and mass are needed. Altitude change comes from the altimeter from the previous group. Distance is calculated from the hall effect sensor on the back bike wheel and from the diameter of the wheel given by the user. The mass is given by the user from the User Interface subsystem. Once the given data is received the following formulas can be used.

  **Convert lbs to kilograms: $$\ \text{kilograms} = \frac {\text{lbs}}  {2.205}$$**

  **$$\ \text{Work} = \text{kilograms} * \text{gravity} * \text{change in altitude}$$**

- Taking these values and creating a matrix for altitude changes we can create a work map by plotting a graph with the X-axis being the current index of the matrix and the Y-axis being the work calculated in joules for the given altitude at the current index of the matrix.

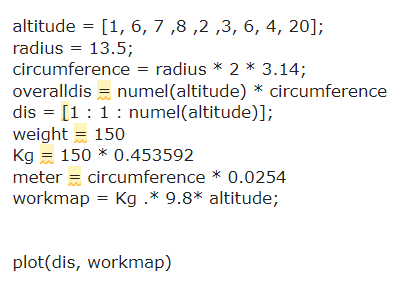
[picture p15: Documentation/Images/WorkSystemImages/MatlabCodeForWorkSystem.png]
MatLab Code


Figure 1. Matlab Code for Work System

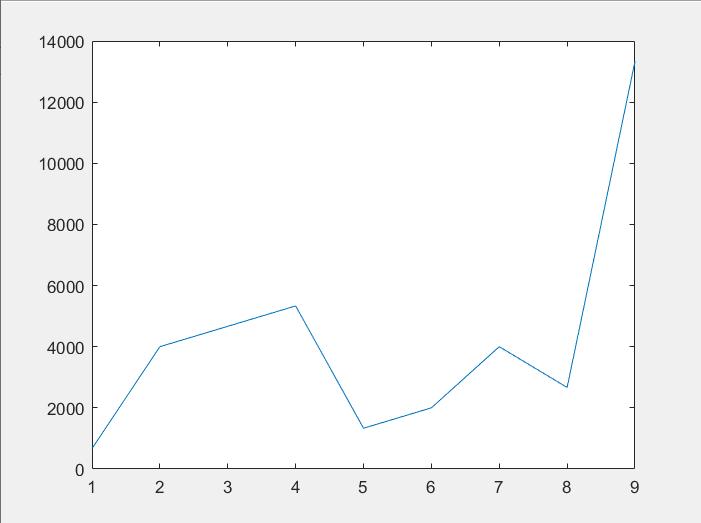
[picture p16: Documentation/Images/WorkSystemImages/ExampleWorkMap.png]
Work Map Example


Figure 2. Example Work Map

## Buildable Schematics

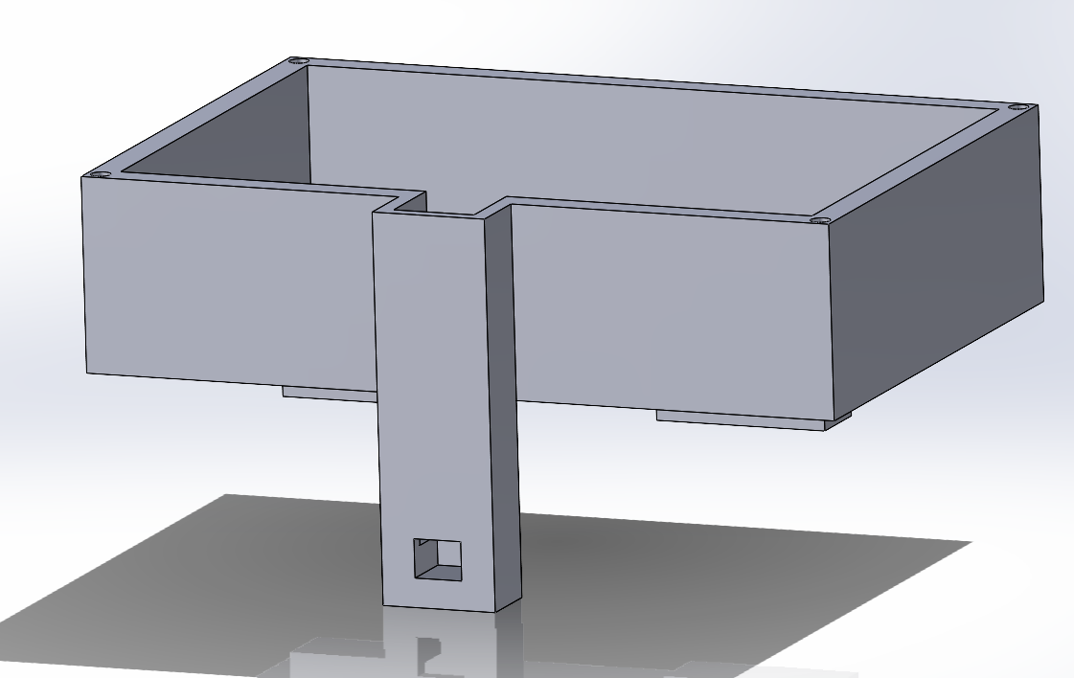
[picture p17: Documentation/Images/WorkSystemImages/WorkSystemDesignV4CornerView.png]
SolidWorks design of work system housing


Figure 3. Housing for Work System

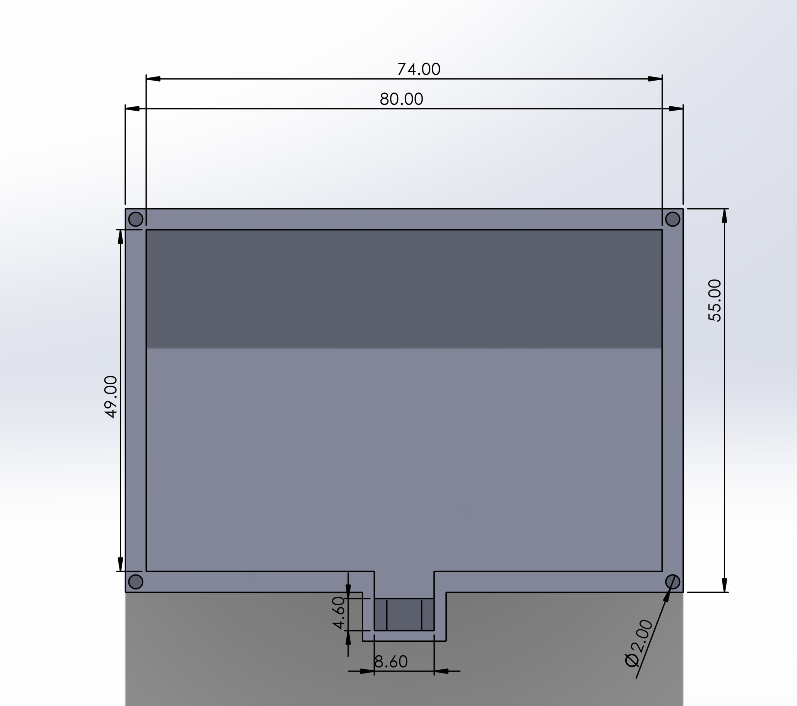
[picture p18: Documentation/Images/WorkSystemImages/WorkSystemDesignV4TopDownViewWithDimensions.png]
Work system housing Top Down


Figure 4. Top Down View With Dimensions

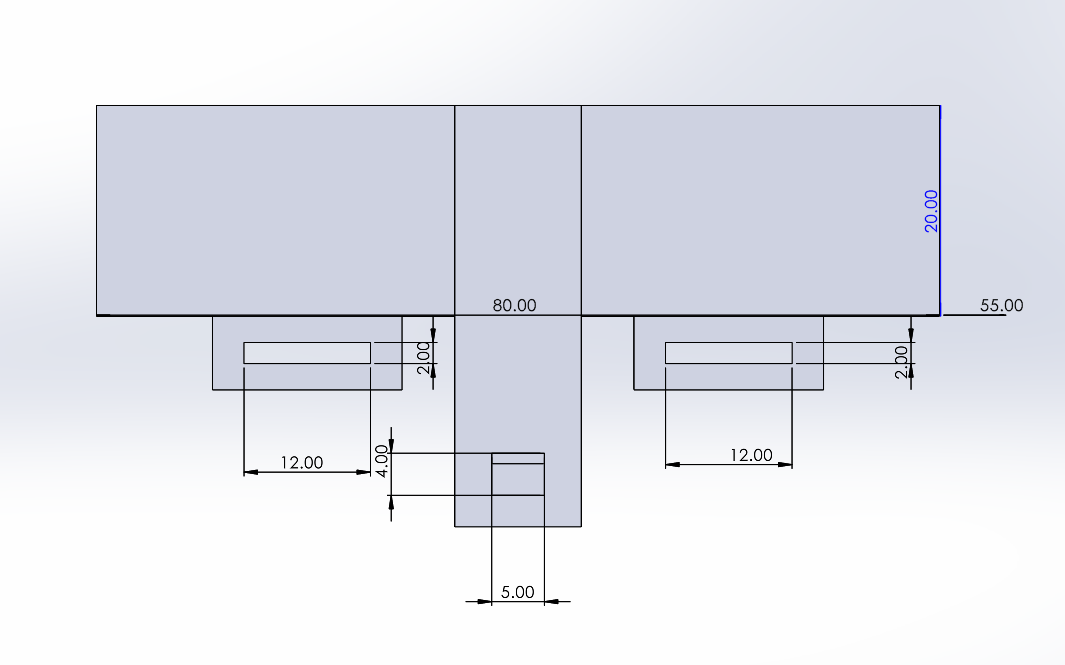
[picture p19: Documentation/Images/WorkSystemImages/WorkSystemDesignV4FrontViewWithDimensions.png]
Work system housing Front Facing


Figure 5. Front-Facing View With Dimensions

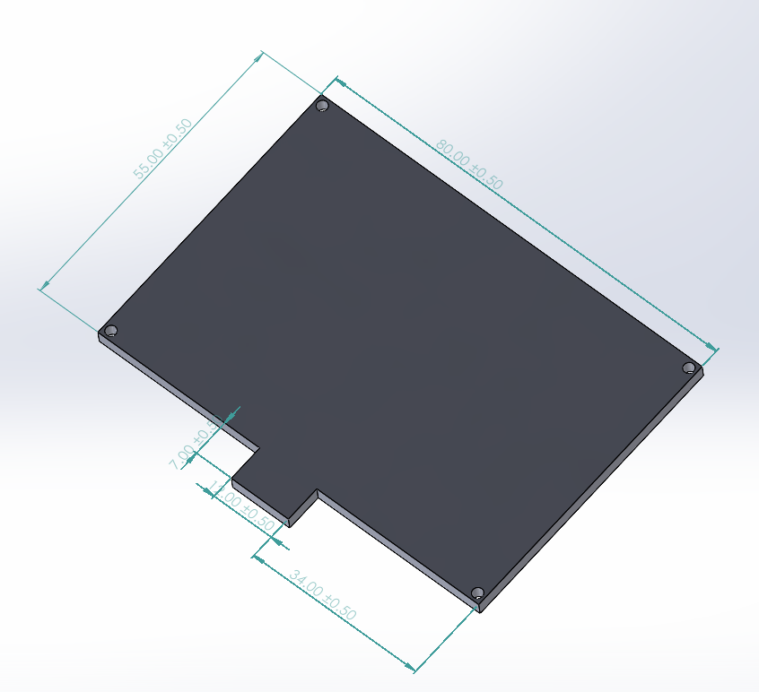
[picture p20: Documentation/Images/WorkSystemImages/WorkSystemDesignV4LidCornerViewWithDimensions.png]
Lid for Housing


Figure 6. Lid for Housing With Dimensions

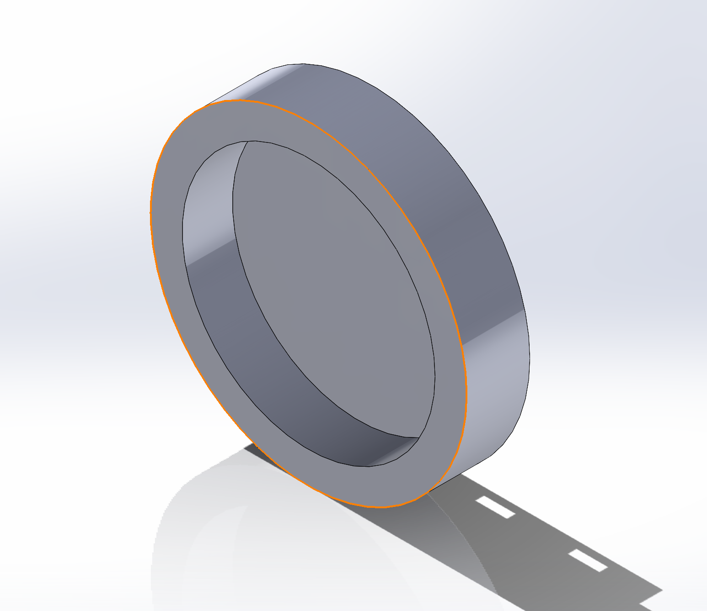
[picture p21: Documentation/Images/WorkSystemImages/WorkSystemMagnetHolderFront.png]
Holder for magnet front


Figure 7. Front View of Magnet Holder for Attachment to Spoke

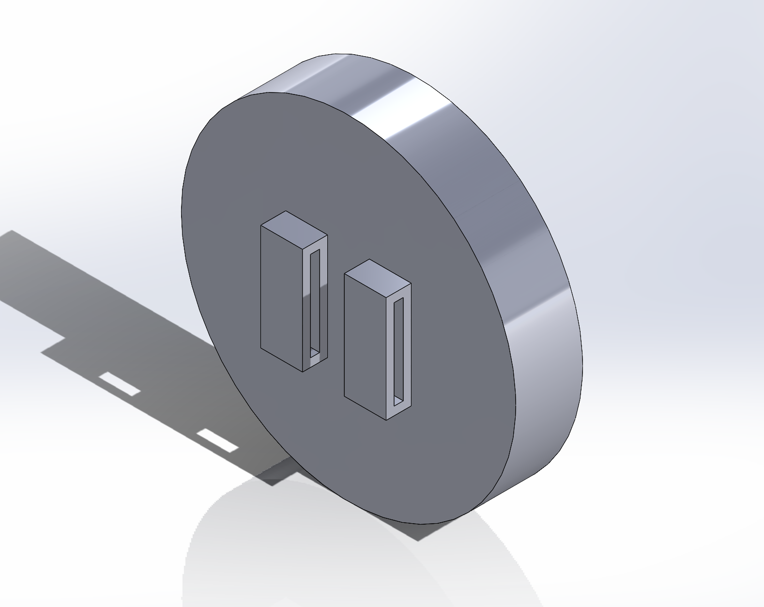
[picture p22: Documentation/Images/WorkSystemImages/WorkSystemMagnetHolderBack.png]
Holder for magnet back


Figure 8. Rear View of Magnet Holder for Attachment to Spoke

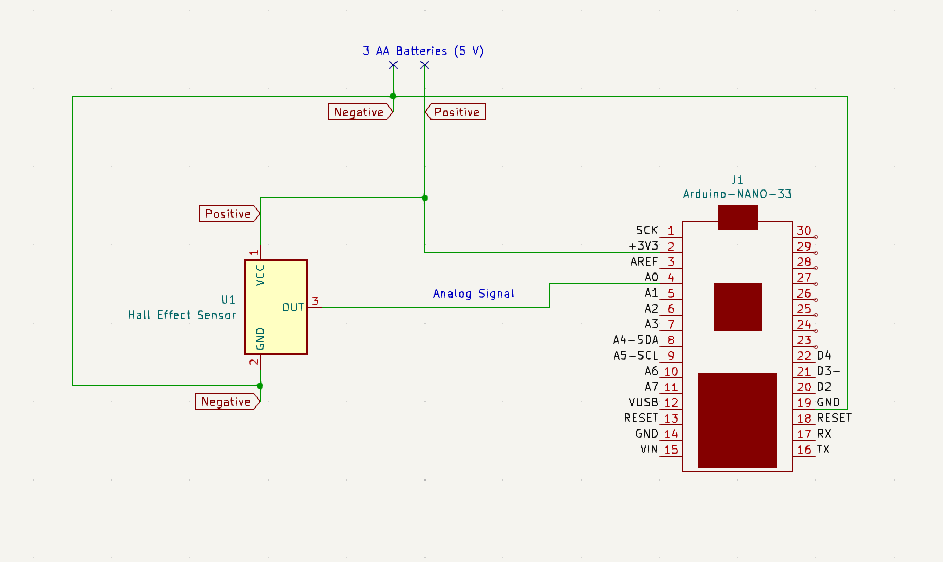
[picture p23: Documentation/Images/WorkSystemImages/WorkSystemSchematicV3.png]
Circuit Schematic


Figure 9. Circuit Schematic of Work System

## Bill of Materials

|Item|Description|Part Number|Manufacturer|Quantity|Individual Price|Total|
|----|---|---|---|---|---|-----|
|Hall Effect Sensor|Hall Effect Sensor Single Axis TO-92-3|DRV5056A2ELPGMQ1|Texas Instruments|2|$2.01|$4.02|
|Arduino Nano 33 BLE |Arduino Nano 33 Bluetooth Low Energy Microcontroller|ABX00030 |Arduino|1|$26.30|$26.30
|AA holder|Battery holder fo 3 AA batteries|BC3AAW-ND|MPD (Memory Protection Devices)|1|$2.33|$2.33|
|Magnet|Nickel-Plated N52 Magnet|DX44-N52|K&J Magnetics|1|$11.57|$11.57|
|Acrylic Sealant (For waterproofing enclosure)|Clear Electronic Grade Silicone - 2.8 oz Squeeze Tube|ASI 388|American Sealants Inc.|1|$11.95|$11.95|
|Conformal Coating (for waterproofing PCB)|CONFORMAL COATING UL 94V-0|419D-55ML|MG Chemicals|1|$16.76|$16.76|
|Total|||Total Components|7|Total Cost|$72.93

## References:

[1]”DRV5056-Q1 Automotive Unipolar Ratiometric Linear Hall Effect Sensor,” https://www.ti.com/lit/ds/symlink/drv5056-q1.pdf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 (accessed Oct. 25th, 2023)

[2]”How do you calculate the magnetic flux density?” https://www.supermagnete.de/eng/faq/How-do-you-calculate-the-magnetic-flux-density (accessed Oct. 25th, 2023)

[3]"BMX Bike Sizing,”  https://rampfest.com.au/pages/bmx-bike-sizing. (accessed Oct. 25th, 2023)

[4]"Bike Tire Sizes Guide," Sweet Pete's. Available: https://www.sweetpetes.com/articles/bike-tire-sizes-guide-pg564.htm. (accessed Oct. 25th, 2023)

[5]E. Jack, Fastest cyclist ever: Setting a World Record speed of 183mph on a bicycle, Cyclist, 2019. https://www.cyclist.co.uk/news/fastest-cyclist-ever-setting-a-world-record-speed-of-183mph-on-a-bicycle

[6]V. David, A Quick Guide to Understand IPC-CC-830B Qualification Standard, HumiSeal, 2018. https://blog.humiseal.com/a-quick-guide-to-understand-ipc-cc-830b-qualification-standard

[7] Energizer Brands LLC, “Cylindrical Primary Lithium Handbook and Application Manual,” Form No. 12004-A.

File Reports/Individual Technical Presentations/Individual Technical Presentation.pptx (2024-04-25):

## Individual Technical Presentation: Magnetic Resonance

Caleb Rozenboom

## Introduction

- MRI changed the medical industry
- Technology advanced in quantum physics, super conductors, and computer science

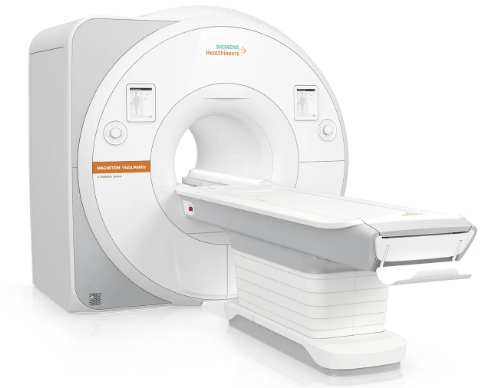
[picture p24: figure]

## History of the MRI

- Harmful X-rays
  - Absorption of x-ray beams
- Low-resolution ultrasound
  - Sound waves bounce off densities
- Flat 2d
- MRI better imaging and contrast with less risk
- Takes longer and expensive


## History of the MRI

- Developed by Isidor Isaac Rabi (1898-1988) [1]
- Worked with Bohr, Pauli, Heisenberg
- Discovered magnetic resonance
- Nobel Prize in 1944
- First images in 1970
- First human subject in 1977
- After being imaged he said, “It was eerie. I saw myself in that machine, I never thought my work would come to this.”


## Hydrogen Atom

- Hydrogen atoms in body
- Bar magnets
- Evenly distributed probability
- Net magnetization vector
- Parallel and anti-parallel


## Nucluear Spin

- Precession
- Larmor Equation
ω=γB
- ω is the Larmor frequency (MHz)
- γ is the gyromagnetic ratio (in MHz/T)
  - Specific to element
- B is the magnetic field strength (T)

## Radiofrequency Pulse

- RF (B1 in right picture)
- Changes longitudinal magnetization vector (LMV)
- Temporarily aligns in phase
- Angle depends on intensity
- Sends radiofrequency back


## Relaxation

- Sends 90 degree RF
  - Transverse Magnetization Vector
- Free induction decay
- T1 time:
  - 63% of LMV has been recovered [2]
- T2 time:
  - 63% of TMV has been lost [2]
- T1 and T2 are unique to different tissues
  - T1 fat and T2 water


## Free Induction Decay Caveats

- Applies to 90 degree only
- Signal decays rapidly
  - Requires fast scanner
- T2* constant dephasing
  - Not actually uniform
  - Experience B field differently
  - Signal dropout
- How to fix? 180 RF correction pulse
- More energy: echo
- Done over and over until no more energy

## Spin Echo Sequence


## References

[1] July, 1977: MRI Uses Fundamental Physics for Clinical Diagnosis https://www.aps.org/publications/apsnews/200607/history.cfm#:~:text=The%20first%20images%20were%20produced,soft%20tissues%20like%20the%20brain.
[2] Questions and Answers in MRI https://mriquestions.com/opposite-effects-uarrt1-uarrt2.html
[3] T1-weighted and T2-weighted MRI image synthesis with convolutional generative adversarial networks https://www.ncbi.nlm.nih.gov/pmc/articles/PMC8086713/#:~:text=T1%2Dweighted%20MRI%20enhances%20the,MRI%20image%20analysis%20and%20diagnosis.

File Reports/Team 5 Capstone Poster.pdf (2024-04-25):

# Ride Replay Kit

Jesse Brewster | Ben Ebel | Jayden Marcom | Caleb Rozenboom | Utsav Singha | Caleb Turney

The Ride Replay Kit will provide users with an accurate recreation of a recorded bike trail and will have a work-map for each trail. A GUI along with an actively changing resistance will be implemented to control the playback and accurately reflect the work done during a recorded trail. The kit will also have audio, visual, and immersion systems to recreate the sounds, video, and wind speed of the trail on the exercise bike.
The Problems and Solutions

Trail Data Recording:

The main problem with trail recording is reading in the work done by a rider over a specific section of time. Another big issue that was identified was how to secure both a microphone and camera on a bike to allow for audio and video recordings.

The solution to the main issue of recording work done by a user was found in using a formula for potential energy based on weight, altitude change, and gravity (U = mgℎ). Using this formula, a sensor for atmospheric pressure, that checks when the wheel has made a full rotation, and an array to store the atmospheric values at specific distances a work map can be created. Using this work map, the work done by a rider can be accurately recorded. The camera and microphone mounting issue was fixed by creating a 3D printed mount for each device that clamped onto the bike handlebars securely.

Trail Recreation:

The first problem was replicating a recorded hill or change in elevation on the exercise bike. The next issue for trail recreation was to find a way to scale the video and audio replay with the user’s speed. The issue with replaying the video through the exercise bike was that the video playback speed needed to scale with the speed of the user, while also maintaining smooth visuals while going slower than the initial recording. The issue with replaying the audio was the playback speed of the user may vary from the recorded speed thus causing the audio to be sped up and pitched differently than the original recording. The final problem was recreating the feeling of wind.

The solution for the problem of recreating elevation changes accurately is to take the input from a force sensor attached to the bike pedals. This would calculate the work being inputted by the user. The work values from the user's input are summed together in real time and compared to the work map mentioned in the previous section. The goal is to replicate the work done on the trail by changing an actuator that either increases or decrease the back wheel’s resistance depending on the current value of the work map. The solution for the video playback was to use interpolated frames allowing the user to go slower without loss of visual smoothness. The solution for the audio playback was to loop the audio over a specific time until the user has progressed past that section. The final solution for recreating wind was to use a fan to simulate airflow for a realistic feeling immersive experience.

e

Python programming language - Used in every aspect of the project to interpret the work data and react accordingly to replicate the recorded trail accurately.

VLC player - Used to vary video playback speeds, and for the playback and looping of particular audio files.

Ableton Live 11 - Used for audio processing and high/low-pass filters.

Flow Frames- Used to interpolate frames and remove duplicate frames

Tkinter - Used to create the User Interface

Final BOM

This is the final BOM for the project. However, this is not the full cost of the project since many of the devices used are from the previous two Mario Kart Teams.

Future Work

There are many ways to continue this project. One way is to improve upon the process that the audio segments are split up. Another aspect that could be improved is the visual fidelity. The work system could use a complete redesign of the 3D prints to fit more bikes. The User Interface could be made more visually appealing. The back actuator could receive more precise inputs from the resistance calculations.

Acknowledgements

We would like to thank Professor Roberts and other faculty for giving us the opportunity to work on this project. We would also like to thank all the people that helped us during this project.

### Conceptual Analysis

The most interesting result from the conceptual analysis is the result from the calculations of work recreation on the exercise bike. The equation that resulted was a relation between the work from the work map in joules and the actuators distance from the back wheel. The equations used are as follows:

The most important result from the experiments is the comparison of the generated work map to the actual work done during the same trail ride. To do this experiment a work map was generated for a specific trail and the total amount of joules was compared to the total amount of joules expended by two people riding the same trail multiple times.

Figure 1. Camera and Microphone 3D Model

Figure 3. Spectrogram of trail audio for analysis
over time | Figure 4. Block Diagram of the Design
*Force Formula | *Magnetization | *Magnetic Dipole

Using these Formulas

*New Formula for actuator
distance based on work

0

10

20

30

40

50

60

1 | 2 | 3 | 4 | 5

Work (Actual vs Measured)

Rider 1 | Rider 2 | Work Measured | Linear (Work Measured)

Figure 5. Graph of the new formula for actuator distance

Figure 8. Graph of the new formula
for actuator distance

Figure 7 Circuit holder for Work map creation

Figure 6. Holder for force sensors on pedal of exercise bike

Figure 9. User Interface displayed on monitor

Figure 2. Circuit for recreation of windspeed

Figure 10. Exercise bike with all items attached

Objectives

### Experimental Results

### Software

Future Work

### Conceptual Analysis

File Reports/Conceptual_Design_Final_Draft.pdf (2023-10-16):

# Team 5 - Ride Replay Kit

Benjamin Ebel
Electrical and Computer
Engineering Department
Tennessee Technological University Cookeville, TN
baebel43@tntech.edu

Jayden Marcom
Electrical and Computer
Engineering Department
Tennessee Technological University Cookeville, TN
jtmarcom42@tntech.edu

Utsav Singha
Electrical and Computer
Engineering Department
Tennessee Technological University Cookeville, TN
usingha42@tntech.edu

Jesse Brewster
Electrical and Computer
Engineering Department
Tennessee Technological University Cookeville, TN
jibrewster42@tntech.edu

Caleb Rozenboom
Electrical and Computer
Engineering Department
Tennessee Technological University Cookeville, TN
cmrozenboo42@tntech.edu
I. INTRODUCTION
Currently there are no commercially available devices that officially allow for personal recordings of bike trails to be uploaded or shared to other users. The Ride Replay Kit will provide users with an accurate recreation of a recorded bike trail and will have a work-map for each trail, which will be calculated within the Resistance System. The kit will also have audio and visual systems to recreate the sounds and video of the trail on the exercise bike. Additionally, an actively changing resistance will be implemented to accurately reflect the work done during a recorded trail. The last new addition to the kit will be a difficulty system that tailors trails to the experience level of the user. This will be part of making changes to the exercise bike user interface which will also include informing the user of time spent riding the bike. The project will also have to abide by industry regulations, ethical considerations, and broader impacts of the Ride Replay Kit.
A. Identified Problems
The Work System shall provide a unique work-map dependent on the trail. The work subsystem should be accurate to the visual experience and be consistent with the actual work done by the trail rider proportional to the weight of the user. The Visual System shall provide users with a smooth visual experience. The visual experience should allow users to operate the bike without inducing headaches or nausea. The visual experience will also scale with the pace of the user. Team 5 set a constraint to record at minimum of 60 FPS. The Audio System shall provide an appropriate output given the current state of the trail being ridden. The audio should create an immersive experience for the user that is synced with the video playback from the previous system. Audio playback will also scale alongside the video playback depending on the pace of the user. Team 5 set a constraint to limit speaker output to 80 dB in order to not cause hearing damage to the user [1]. Team 5 also established a constraint to match the audio wavelength input from the trail with the audio output wavelength from the trail. This constraint was set to ensure accurate audio feedback during a trail replay.
The Resistance System will change depending upon the effort put in by the user. This will change resistance of the bike to provide users with a way to complete a trail at desired pace while still doing the entirety of the work of that trail. The User Interface of the exercise bike will ask the user to input weight, remind the user of recommended periods of exertion, and select a difficulty option. The weight input of the user will be used for the calculation of work done during the trail. The difficulty option within the user interface will change the overall work done during a replay of the trail. This will give the user the ability to experience the trail at an adequate difficulty level. To accomplish this Team 5 will implement multiple difficulties that adjust the values of the work map of the exercise bike to change the overall work done. The user interface shall remind the user of the recommended time spent on the bike after every trail. Team 5 is setting a constraint to limit maximum latency to 300 ms [2]. This constraint was chosen to meet acceptable latency levels for touchscreen tapping tasks.

II. ETHICAL, PROFESSIONAL, AND STANDARD CONSIDERATIONS

As beneficial as exercise is to the body, it is only beneficial up to a certain point. Exercising too much can actually cause the opposite intended effect of exercise. Over-training can lead to negative health effects, including fatigue, depression, loss of motivation, hypertension, weight loss, and anorexia [3]. Taking this ethical consideration into account, this is the reason for the constraint of the acknowledgment button after every ride [4].

Exposure to high decibels for certain periods of time can cause irreparable hearing damage. Even exposure to relatively lower decibel ranges can be harmful if subjected to long enough periods of time. OSHA limits exposure to 85 dB at or below 8 hours. This constitutes the need for a dB limit for the audio subsystem. Team 5 has set this value to be at or below 80 dB to stay within known safety specifications [5]. This is intended in the event that the Ride Replay Kit is installed in commercial gyms, resulting in employees being exposed to the sounds for long periods of time.
There is currently an exposed flywheel and actuator on the Ride Replay Kit. OSHA requires guards protecting the user from rotating or moving parts of equipment, of which the bike has both [6]. Team 5 will encase the components in question to comply with this standard.
The goal of the Ride Replay Kit is to be immersive for the user, and to give an accurate simulation of the trails recorded. Since this is the goal it could cause a negative affect on tourism within the areas surrounding the bike trails. For instance a user who could have potentially gone to one of the locations to ride the trail may no longer do so due to ease of access of the trail on the Ride Replay kit. To combat this Team 5 will include pictures of the towns or areas nearby the trails after it has been completed to promote tourism. The user would have to interact with the menu to acknowledge that the advertisement has been seen.


Fig. 1. Overall Block Diagram

III. SYSTEM DESIGN
The Ride Replay Kit is split into 5 subsystems, all interacting and influencing each other. These subsystems are work, resistance, user interface, visual, and audio. The Work subsystem calculates the work done by the rider recording the trail and then compares this data to the work done by the user replaying the trail. This data goes to the Resistance subsystem to make sure the work done on the trail remains the same even if the user were to exceed or fail to match the original pace of the rider. The user interface takes in data, displays information, and relays the user’s data to the work calculations. Finally, the Audio and Visual subsystems provide the visual and audio components to make the ride experience as immersive as possible.


Fig. 2. Work System

A. Subsystem 1: Work

The work will be calculated on the trail by using the elevation and distance of the trail, along with the weight of the user provided from the user interface. This work data will provide the comparative value that the resistance subsystem uses to stay consistent with the ride. As the user rides through the virtual trail, the work done will be calculated and sent to a Raspberry Pi, which will then change the resistance to keep the work done and the work recorded equal. The work-map will be created from work calculated and sent to Bluetooth outputs.


Fig. 3. Resistance System

B. Subsystem 2: Resistance

The resistance subsystem will be a closed-loop feedback system in tandem with the work calculations. The output of the resistance subsystem is the actuator which changes the resistance of the bike based on the distance between the two magnets on the actuator and the aluminum flywheel attached to the exercise bike. The actuator distance will be calculated in a Raspberry Pi based on force input on the bike and the current resistance. The velocity will be taken based on rotations per minute of the back tire on the exercise bike. The map will change position based on velocity and change the resistance value accordingly. There must also be a minimum and maximum resistance value to maintain accurate total work done during the replay of a trail.


Fig. 4. Audio System

C. Subsystem 3: Audio

To add to the immersion of the bike, the audio subsystem must be integrated alongside the visual subsystem. The microphone on the Ride Replay Kit will record and stay in sync with the camera. The audio data will be processed by a Raspberry Pi and output to speakers on the exercise bike. The audio subsystem will also have to be interpolated based on the speed of the user and must stay in sync with the visual playback. Headphones may also be added to provide more variety and variability in the user’s experience.


Fig. 5. Visual System

D. Subsystem 4: Visual

The Ride Replay Kit would not be complete without proper visuals. The visual subsystem keeps the user immersed in the virtual trail by updating the current location on the trail based on the current velocity from the resistance subsystem. The visual data from the trail camera will be processed by a Raspberry Pi, which then outputs to the monitor. Based on what speed the user rides the trail, a Raspberry Pi will have to interpolate between frames to provide a smooth playback.


Fig. 6. User Interface

E. Subsystem 5: User Interface
The user will be prompted with two inputs which the Ride Replay Kit will use to calculate the total work done and the resistance as the distance value changes. The first input will be the weight of the user. This will be used to calculate the work-map in a Raspberry Pi and adjust the resistance values accordingly. The second input will be the difficulty level. This will be added for users with the inability to complete trails at a realistic level but still wish to have a comparable ride experience that matches the current fitness goals of the user. Based on the difficulty the user selects, the work done will be scaled down, which will also decrease the net resistance. The user interface will also remind the user after every trail of the appropriate amount of time spent exercising, prompting the user with an acknowledgment button. This will ensure the health and safety by preventing the user from over training and injury [3]. Finally, the user interface will show the user information about the trail ridden and the surrounding area in hope to promote tourism to areas affected by the Ride Replay Kit.

IV. ANALYTIC METHODS OF SUBSYSTEM VERIFICATION

A. Subsystem 1: Work Calculation
The work calculation subsystem will utilize CAD software to simulate work based on distance, elevation, and weight. Using this information, a work-map can be created. To simulate work per interval, a range of realistic distance and elevation values will be used in the software to accommodate for the various trails the system will experience. Then, similar to the user inputting weight into the user interface, generating the specific work-map, a range of weight values will be used to ensure accurate work is calculated throughout the simulation.
B. Subsystem 2: Resistance System
The resistance subsystem will be verified using control system simulation software. The work profile required to complete a trail will first be calculated. The exercise bike and linear actuator will then be simulated in the software per the specifications of the exercise bike and the actuator.

Team 5 will model the bike at the highest resistance of the actuator and the lowest resistance of the actuator to find the minimum and maximum amount of work possible for the bike. These will then be used to format the work profile within these bounds. This is to ensure that whether the user is going faster or slower than the original trail, the work profile will scale within these bounds to ensure the correct amount of work is done and is physically possible based on the bike and actuator specifications.

C. Subsystem 3: User Interface
Using the specifications of the Raspberry Pi, the amount of time for an instruction to be executed by the CPU will be calculated. Using this time, Team 5 will calculate the maximum amount of instructions possible to be executed without causing the processor to have a delay of longer than 300 ms [2]. The code for the graphical user interface will then be limited to this amount of instructions in order to maintain a smooth interaction between the user and the system.
D. Subsystem 4: Visual
Using the data sheets from the Raspberry Pi and camera on the Ride Replay Kit, the visual subsystem output can be calculated. Team 5 will ensure the specifications are within range of the project’s design, specifically the frames per second is at or above 60 fps. Additionally, visual interpolation software with the ability to meet the specifications of a smooth playback at 60 fps will be found and verified using the specifications of the software.
E. Subsystem 5: Audio
To ensure the audio subsystem is verified Team 5 will use the specifications from the microphone and speaker data sheets. The microphone data sheet will be checked to verify that it is omnidirectional to ensure it will pick up audio in a wide area. Additionally, the speaker data sheet will be checked to verify that it is or can be limited to 80 dB to ensure the safety of the user. This means that the system will not only pick up the wide array of sounds on the trail when it is actually put into practice but the speakers will also have the ability to output a safe dB level for the user.
V. CONCLUSION

Team 5’s Ride Replay Kit was designed to give an immersive simulated bike trail experience that will allow the user to personally record bike trails and replay them completely with real-time feedback. The built-in dynamic Resistance System will accurately replicate the physical demands of actual bike trails by simulating changes in elevation and will be customizable for varying fitness levels. The user will also get feedback on how much work has been accomplished after the trail is complete. The Audio and Visual systems will be synced to simulate the trail environment and sounds that the user would experience on the actual trail. This prioritizes user immersion and entertainment making the replay of the trail enjoyable. Automatic post-ride messages will emphasize exercise duration within health limits to promote user safety. The kit’s customizable difficulty options will cater to users of most fitness levels, enhancing accessibility and engagement. Overall, the goal of Team 5’s Ride Replay Kit is to officially give users the ability to replay and share personal recordings of bike trails.

REFERENCES

[1] “Loud noise dangers,” https://www.asha.org/public/hearing/loud-noisedangers. (accessed Oct 4th 2023)/.
[2] W. Ritter, G. Kempter, and T. Werner, User-Acceptance of Latency in Touch Interactions. Cham, CH: Springer International Publishing, 2015.
[3] K. Jeffery and S. Jennifer, Overtraining syndrome: a practical guide. Sports Health, 2012.
[4] “How long to ride a stationary bike for improved fitness,” https://www.onepeloton.com/blog/workout-length (accessed Oct. 4th, 2023)/.
[5] “Occupational | safety | and | health | administration,”
https://www.osha.gov/noise (accessed Oct. 4th, 2023)/.
[6] “Occupational safety and health administration,” Available at https://www.osha.gov/noise.

VI. APPENDIX


Fig. 7. Gantt Chart

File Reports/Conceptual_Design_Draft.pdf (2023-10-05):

# Team 5 - Ride Replay Kit

Benjamin Ebel
Electrical and Computer
Engineering Department
Tennessee Technological University Cookeville, TN
baebel43@tntech.edu

Jayden Marcom
Electrical and Computer
Engineering Department
Tennessee Technological University Cookeville, TN
jtmarcom42@tntech.edu

Utsav Singha
Electrical and Computer
Engineering Department
Tennessee Technological University Cookeville, TN
usingha42@tntech.edu

Jesse Brewster
Electrical and Computer
Engineering Department
Tennessee Technological University Cookeville, TN
jibrewster42@tntech.edu

Caleb Rozenboom
Electrical and Computer
Engineering Department
Tennessee Technological University Cookeville, TN
cmrozenboo42@tntech.edu
I. INTRODUCTION
Team 5’s Ride Replay Kit is creating a re-playable trail experience for users to enjoy from their homes. Team 5’s kit will provide users with an accurate recreation of the bike trail and will have a ”work map” for each recorded trail, which will be calculated within the Resistance System. The kit will also have audio and visual systems to recreate the trail’s sounds and video on the exercise bike. Additionally, an actively changing resistance will be implemented to accurately reflect the work done during a recorded trail. The last new addition to the kit will be a difficulty that allows the user to tailor trails to their experience level this will be part of making changes to the exercise bike user interface which will also include informing the user of their time spent riding the bike. The project will also have to abide by regulations set by professional, ethical, and broader considerations.
A. Identified Problems
The Work System shall provide a unique work map dependent on the trail. The Work System should be accurate to the visual experience and be consistent with the actual work done by the trail rider proportional to the user’s weight. To accomplish this team 5 will measure distance and elevation, then calculate work done on a trail for each user.
The video feedback system shall provide users with a smooth visual experience. The visual experience should allow users to operate the bike without inducing headaches or nausea. The visual experience will also scale with the user’s pace. To accomplish this Team 5 set a constraint to record at minimum of 60 FPS.
The audio feedback system shall provide an appropriate output given the current state of the trail being ridden. The audio should create an immersive experience for the user that is synced with the video playback from the previous system. Audio playback will also scale alongside the video playback with the user’s pace. To accomplish this Team 5 set a constraint to limit speaker output to 80 dB. This constraint is in order to not cause hearing damage to the user [1]. Team 5 also established a constraint to match the audio wavelength input from the trail with the audio output wavelength from the trail. This constraint was set to ensure accurate audio feedback during a trail replay.
The resistance will change depending upon the effort put in by the user. The changing resistance shall provide users with a way to complete a trail at their desired pace while keeping the work done during the ride comparable to the recorded work done. To accomplish this Team 5 will monitor the pace of the user and scale the output accordingly.
The changes to the user interface of the exercise bike will ask the user to input their weight, will remind the user of recommended periods of exertion, and allow for the choice of difficulty. Inputting the user’s weight will allow for the calculation of work done during a trail. The difficulty choice will tell the Raspberry Pi what difficulty to calculate for and scale it accordingly. The user interface shall remind the user of the recommended time spent on the bike after every trail. To accomplish these tasks Team 5 is adding code to the existing user interface implemented by the previous iterations. Team 5 is setting a constraint to limit maximum latency to 300 ms. This constraint was chosen to meet acceptable latency levels for tapping tasks.
The difficulty option within the user interface will change the overall work done during a replay of the trail. This should create additional options for users who cannot bike a difficult trail giving them the ability to experience it at a level adequate for them. This will also allow users who want a realistic experience to get work comparable to the work they would experience on the actual trail. To accomplish this Team 5 will implement multiple difficulties that adjust the values of the actuators of the exercise bike to change the overall work done.

II. ETHICAL, PROFESSIONAL, AND STANDARD CONSIDERATIONS
As beneficial as exercise is to the body, it is only beneficial up to a certain point. Exercising too much can actually cause the opposite intended effect of exercise. Over-training (OTS) can lead to negative health effects, including fatigue, depression, loss of motivation, hypertension, weight loss, and anorexia [2]. Taking this standard consideration into account, this is the reason for the constraint of the acknowledgment button after every ride to prevent OTS [3].
Low frame rate, although not directly harmful, is distracting. Visual appeal is vitally important, especially for a possible marketable product. This is the cause for the frame rate constraint of a minimum value of 60 fps. This will make the user’s trail replay that much more enjoyable and immersive [4].
Exposure to high decibels for certain periods of time can cause irreparable hearing damage. Even exposure to relatively lower decibel ranges can be harmful if subjected to long enough periods of time. OSHA limits exposure to 85 dB at or below 8 hours. This constitutes the need for a dB limit for the audio subsystem, which team 5 has elected to be at or below 80 dB to stay within known safety specifications [5].
For interaction with the user interface, latency must be mitigated to avoid user frustration. This broad consideration is solved by limiting the latency to at most 300 ms. Users will have a smoother interaction with Team 5’s ride replay system overall with this constraint. [6].

III. SYSTEM DESIGN


Fig. 1. Overall Diagram

The Ride Replay Kit is split into 5 subsystems, all interacting and influencing each other. These subsystems are work, resistance, user interface, visual, and audio. The work subsystem calculates the work done by the rider recording the trail and then compares this data to the work done by the user replaying the trail. This data goes to the resistance subsystem to make sure the work done per distance remains the same. The user interface takes in data, displays information, and relays the user’s data to the work calculations. Finally, the audio and visual subsystems provide the visual and audio components to make the ride experience as immersive as possible.


Fig. 2. Work System

A. Subsystem 1: Work

Work will be calculated on the trail by using the elevation and distance of the trail. This information, along with the user’s weight provided from the user interface, will provide the work done over the distance of the ride. This work data will provide the comparative value that the resistance subsystem uses to stay consistent with the ride. As the user rides through the virtual trail, the work done will be calculated and sent to a Raspberry Pi, which will then change the resistance to keep the work done and the work recorded equal.


Fig. 3. Resistance System

B. Subsystem 2: Resistance
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

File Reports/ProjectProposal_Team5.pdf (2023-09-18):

# Team 5 - Mario Kart Bike

Jesse Brewster | Benjamin Ebel
Electrical and Computer Engineering Department | Electrical and Computer Engineering Department
Tennessee Technological University | Tennessee Technological University
Cookeville, TN | Cookeville, TN
jibrewster42@tntech.edu | baebel43@tntech.edu
Caleb Rozenboom | Jayden Marcom
Electrical and Computer Engineering Department | Electrical and Computer Engineering Department
Tennessee Technological University | Tennessee Technological University
Cookeville, TN | Cookeville, TN
cmrozenboo42@tntech.edu | jtmarcom42@tntech.edu
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

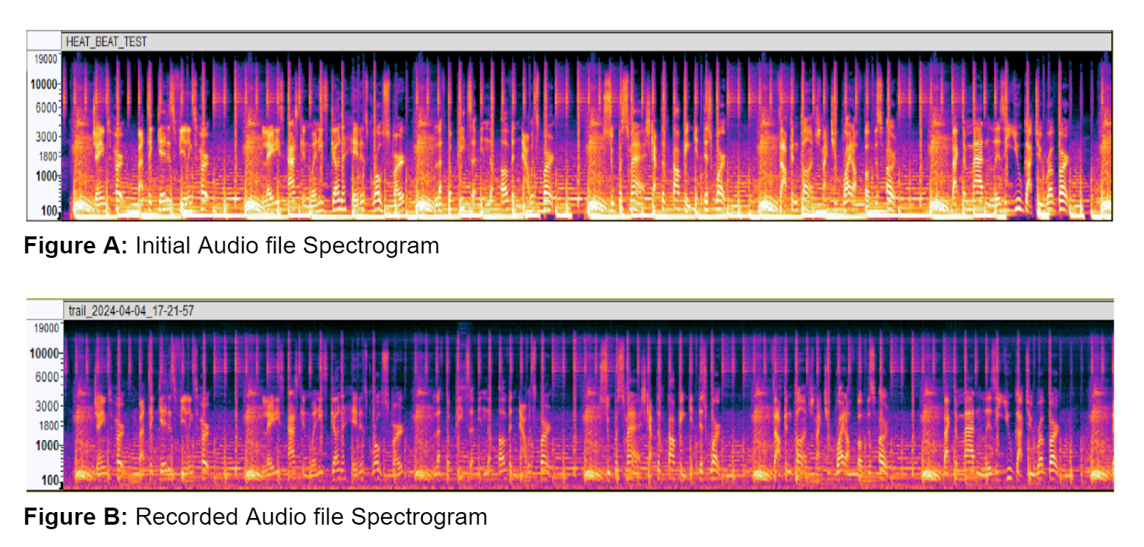
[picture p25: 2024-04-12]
Documentation/Images/AudioAndVideoSystemImages/Spectrogram of Audio File.png

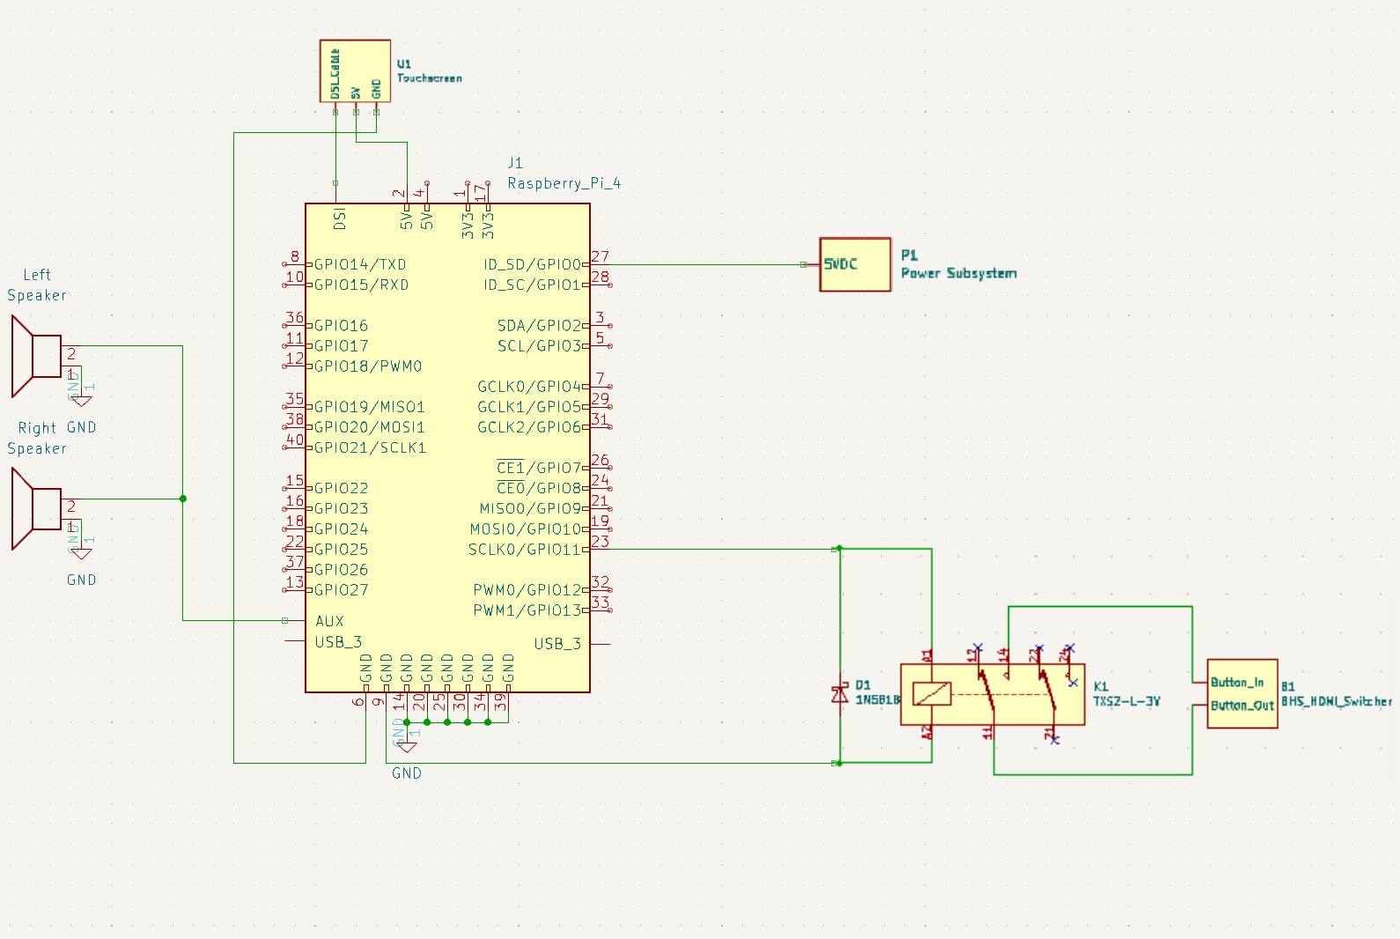
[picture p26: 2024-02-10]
Documentation/Images/AudioAndVideoSystemImages/Speaker Schematic.png

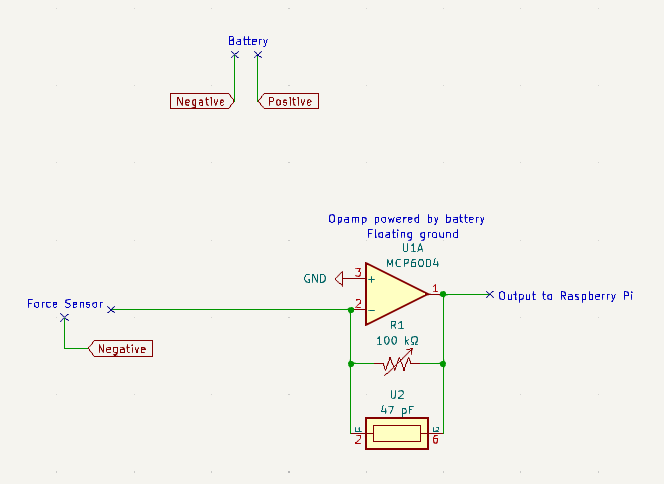
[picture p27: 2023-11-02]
Documentation/Images/ResistanceSystemImages/ResistanceSystemCircuitDesign.png

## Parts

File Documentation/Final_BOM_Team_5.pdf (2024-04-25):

Product Name | Description | Subsystem Used | Part Number | Manufacturer | Quantity Price

OpAmp IC

General Purpose Amplifier 4 Circuit Rail-to-Rail 14-
PDIP | Resistance System | MCP6004-I/P | Microchip Technology | 2 | $1.18

Potentiometer

100 kOhms 0.5W, 1/2W PC Pins Through Hole
Trimmer Potentiometer Cermet 1.0 Turn Top
| Adjustment | Resistance System | 3386P-1-104LF | Bourns Inc | 2 | $3.22
BATT HOLDER AA | Battery Holder (Open) AA 3 Cell Wire Leads - 6"
| (152.4mm) | Resistance System | BC3AAW | MPD | 2 | $4.66
Capacitor | 47 pF Mica Capacitor 500 V Radial | Resistance System | CD15ED470JO3 | Cornell Dubilier Electronics (CDE) | 2 | $3.56

Perfboard

Breadboard, General Purpose Plated Through Hole
(PTH) Pad Per Hole (Round) 0.1" (2.54mm) Grid | Resistance System | ST-PERF-1-2 | SchmalzTech, LLC | 2 | $7.80

Arduino Nano

Arduino Nano 33 Bluetooth Low Energy
Microcontroller | Resistance System | ABX00030 | Arduino | 2 | $55.18

Weight Sensors

8pcs Load Cell 50kg Weight Sensor Half Bridge
Strain Gauge Human Body Digital Scale + 2pcs
| HX711 Amplifier AD Module for Arduino | Resistance System | B09W2K13ZY | DIYmalls | 1 | $10.98
Speaker | Logitech Z207 2.0 Multi Device Stereo Speaker | Audio | B074KJ6JQW | Logitech | 1 | $59.94
Mic Mount | CAMVATE Super Clamp with Cold Shoe Mount for
| Camera Flash Light | Audio | B07D9LTNG9 | CAMVATE | 1 | $15.00
Microphone | Logitech Blue Snowball
| USB Microphone for PC | Audio | B000EOPQ7E | Logitech | 1 | $69.99
Windshield for Microphone | Deadcat Windshield
| Wind Cover for Blue
| Snowball iCE | Audio | B07SF5C6BV | YOUSHARES | 1 | $9.99
Microphone Mount Adapter | 5/8"-27 Male Threaded
| Cold Shoe Adapter for
| Microphone Mount | Audio | B014XGA4DE | CAMVATE | 1 | $5.99

Pole Mount

Universal Stainless Steel
Vertical Pole Mount
Adapterwith 3 Loops | Audio | B0BVT4J3FF | Lighfast | 1 | $9.99

Screws

1/4-20 x 3/4" Button
Head Socket Cap Bolts
Screws, 304 Stainless
Steel 18-8 | Audio | B0BVT4J3FF | EastLo | 1 | $7.99

Shock Mount for
Microphone

YOUSHARES Snowball
Shock Mount,
Shockmount Reduces
Vibration Noise
Matching Mic Boom Arm
Stand, Compatible with
Blue Snowball iCE USB
| Microphone | Audio | B08L4DB79P | YOUSHARES | 1 | $16.88
Hall Effect Sensor | Hall Effect Sensor Single Axis TO-92-3 | Work | DRV5056A2ELPGMQ1 | Texas Instruments | 2 | $4.02
Arduino Nano | Arduino Nano 33 BLE with Headers
| [ABX00034] | Work | TIFC00125 | Arduino | 2 | $59.98
BATT HOLDER AA | Battery holder fo 3 AA batteries | Work | BC3AAW-ND | MPD (Memory Protection Devices) | 1 | $2.33
Magnet | Nickel-Plated N52 Magnet | Work | B0CGDTQ64C | Mixia | 2 | $26.99

Power Supply

DC 12 Volt 5 Amp Power Supply 60W 12Volt 5Amp AC Adapter 100-240V 50-60Hz AC to DC 12V 5A
Power Adapter Converter with 5.5mm x 2.5mm Tip
& 1 Female Terminal for LED Strip Light CCTV
Camera etc. | Immersion | B0BJVVBBMJ | Amazon | 1 | $10.87

Fans

Fan Tubeaxial 12VDC Square - 120mm L x
120mm H Ball 185.5 CFM (5.19m³/min) 4 Wire
| Leads | Immersion | CFM-A225BF-158-597-22 | DigiKey | 2 | $71.70
Arduino Mega 3 | Arduino Mega 2560 REV3 [A000067] | Immersion | B0046AMGW0 | ARDUINO | 1 | $48.90
TOTAL COST: | $507.14
TOTAL QUANTITY: | 31

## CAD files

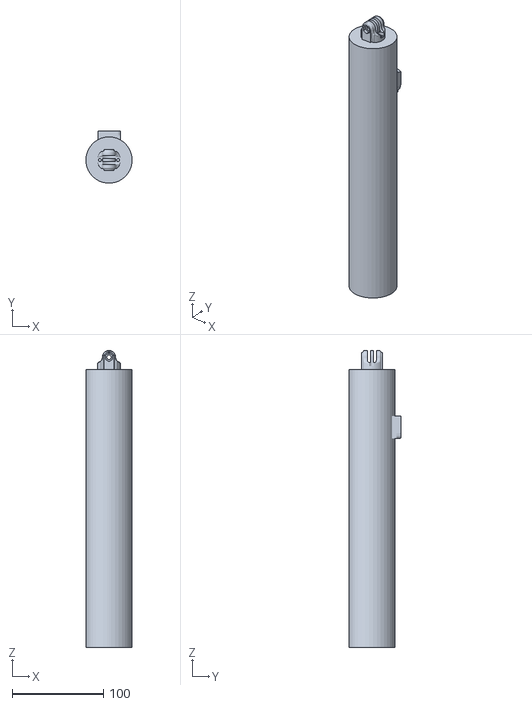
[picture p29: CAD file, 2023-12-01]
Documentation/3D Models/AudioAndVideoSystem3DModels/Camera and Mic mount - Whole Part.STL
50.8 x 57.5 x 325.8

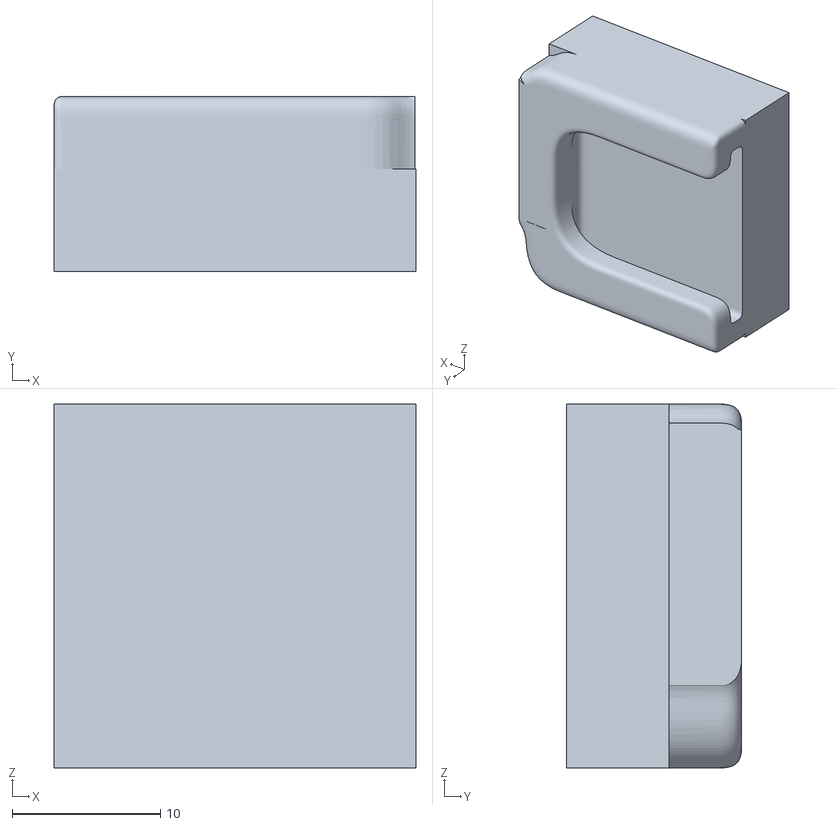
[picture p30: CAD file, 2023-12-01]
Documentation/3D Models/AudioAndVideoSystem3DModels/Camera and Mic mount - cold shoe boop-1.STL
24.4 x 11.8 x 24.5

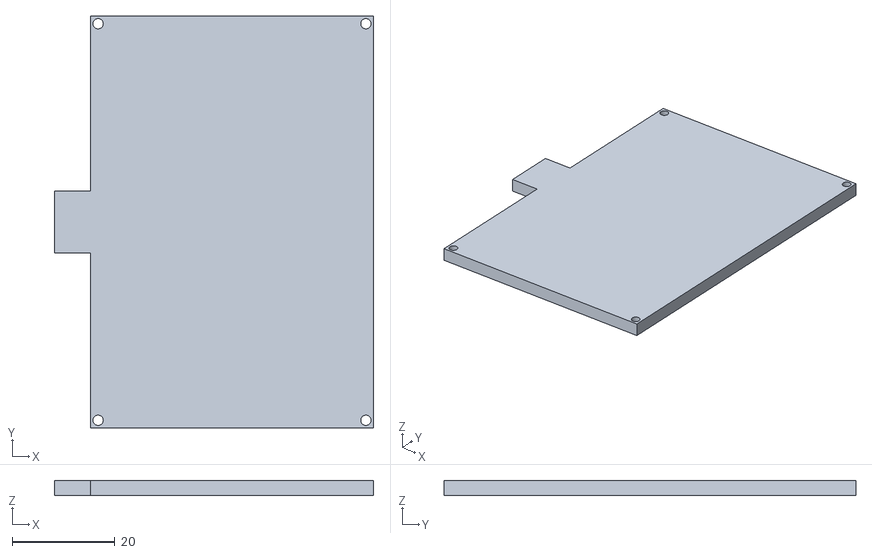
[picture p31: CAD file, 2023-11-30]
Documentation/3D Models/WorkSystem3DModels/WorkSystemLidV4.STL
62.0 x 80.0 x 3.00

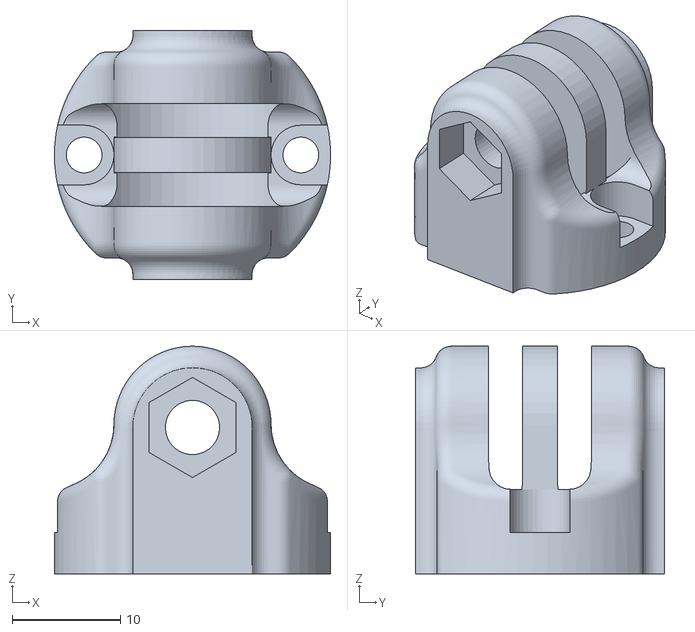
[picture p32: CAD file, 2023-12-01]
Documentation/3D Models/AudioAndVideoSystem3DModels/Camera and Mic mount - Gopro_6dz2-1.STL
25.5 x 23.0 x 21.0

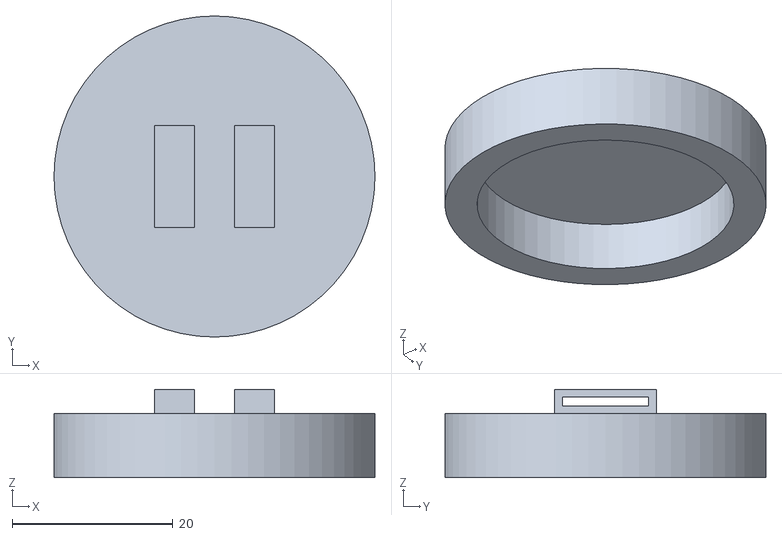
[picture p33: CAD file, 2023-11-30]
Documentation/3D Models/WorkSystem3DModels/Magnet_Mount.STL
40.0 x 40.0 x 11.0

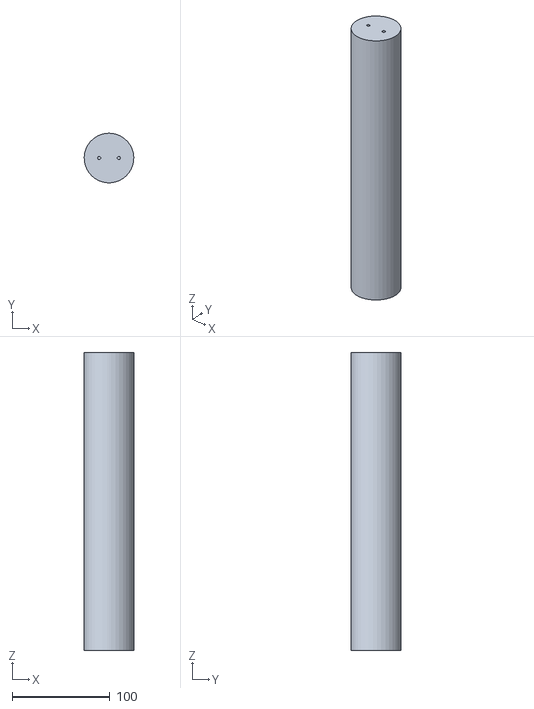
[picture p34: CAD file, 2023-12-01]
Documentation/3D Models/AudioAndVideoSystem3DModels/Camera and Mic mount - Holder-1.STL
50.8 x 50.8 x 304.8

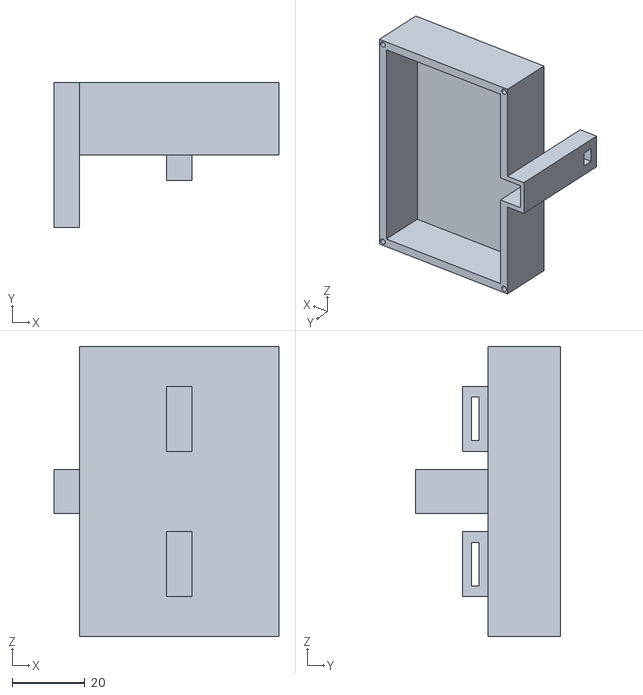
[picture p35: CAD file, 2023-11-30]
Documentation/3D Models/WorkSystem3DModels/WorkSystemDesignBoxV4.STL
62.0 x 40.0 x 80.0

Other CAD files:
Reports/Poster Template/Images/INN_Topology.dwg

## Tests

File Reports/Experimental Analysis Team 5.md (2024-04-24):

# Team 5 - Ride Replay Kit
## Team Members: Benjamin Ebel, Caleb Rozenboom, Caleb Turney, Jayden Marcom, Jesse Brewster, Utsav Singha

## Experimentation

### GUI Subsystem - Benjamin Ebel

| Item | Testing Method |Expected Results | Actual Results | Was The Constraint Fulfilled |
|---|---|---|---|---|
|Overexertion Reminder|Using the time library in Python we can see how long a piece of code or function has been running. Using this a variable was created for detecting how long the user has been riding and at the 2-hour mark a pop-up window appears pausing the trail and alerting the user that they have been riding for over 2 hours. The message box then asks them to acknowledge that if they continue to ride it could possibly cause damage to their muscles. After the trail has been started a time variable starts counting up in seconds and once it gets to 7200 seconds the pop-up window appears alerting the user and won’t continue until they press ok on the window. To test this I will set the time variable to 7140 seconds to allow replay for a minute and then at the minute mark the pop-up window will appear. I will then press the button to attempt to bypass the window. I will then pedal the bike to attempt to bypass the window.|I expect that for this test user will ride for the minute and at the end of the minute a message box will appear on the screen asking them to acknowledge that they have been riding for 2 hours and it will not allow them to continue riding until the ok button on the message box is clicked.|The pop-up window then appeared alerting the user of the risk of overexertion. Attempting to press the main UI will only cause the screen to blink twice and not allow any interactions. Attempting to pedal does not unpause the trail and the message remains on the screen. The only way to continue the trail video is to press the ok button on the pop-up menu.|Yes|
#### Over Exertion Reminder

| Item | Testing Method |Expected Results | Actual Results | Was The Constraint Fulfilled |
|---|---|---|---|---|
|Loading Screen/Interaction Latency/User Interrupt|Using the time library in Python we can see how long a piece of code or function has been running. I set a start time variable to start at the beginning of a function call and an end time variable to store the value of the time at the end of the function call. Once this had been done I took the end time minus the start time to get the result of how long the function took to run. If one of these tests takes longer than 300ms to run a loading screen was put in place to alert the user that their input has been seen and will be handled soon.|I expect that all functions will be under the 300ms execution time and the system will not need to add a loading screen to any interactions.|Almost every function in the GUI had less than 300ms execution time except for loading the video. I tested the play video function with a short video of around 5 minutes and a 4-hour-long trail ride and both of these tests resulted in a latency of longer than a second. Since this is longer than the allowed latency of 300ms I put in a loading screen to ensure the user was aware their input had been seen. These test latencies can be seen under the Latency Graph header below.|Yes|
#### Latency Graphs
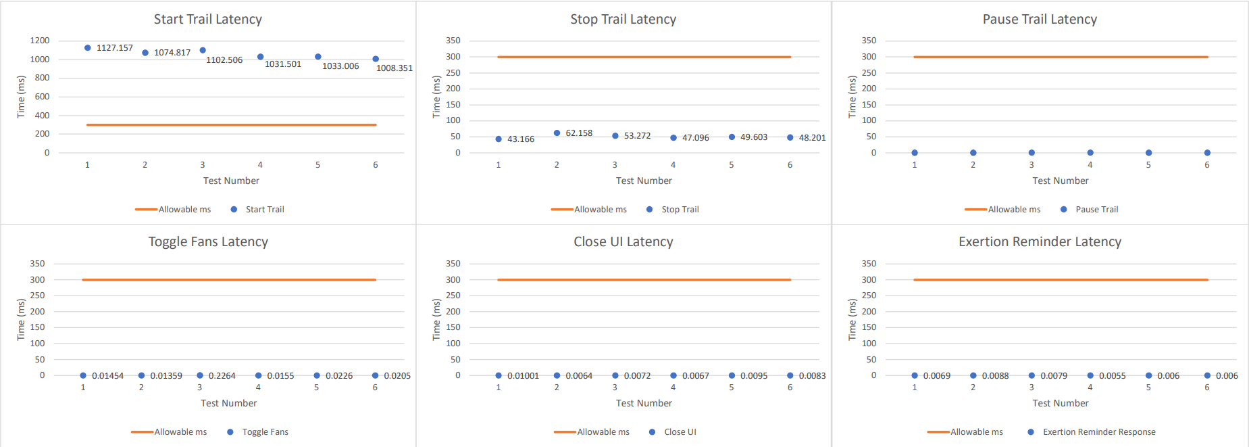
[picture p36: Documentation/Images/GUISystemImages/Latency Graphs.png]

| Item | Testing Method |Expected Results | Actual Results | Was The Constraint Fulfilled |
|---|---|---|---|---|
|Color Blindness Sensitivity|I will take a picture of the GUI using an iPhone camera. Then I will edit a black-and-white filter over it using the built-in filters on the iPhone. This will ensure that everything on the GUI can still be read by users with the harshest kind of color blindness which is total color blindness.|Since the GUI is already grey and black I believe that there will be no issue with any color-blind person using the GUI.|Using the photos below under the Color Blind Photos Test header, it can be seen that the UI would still be visible to someone who had complete color blindness.|Yes|
#### Color Blind Photos Test
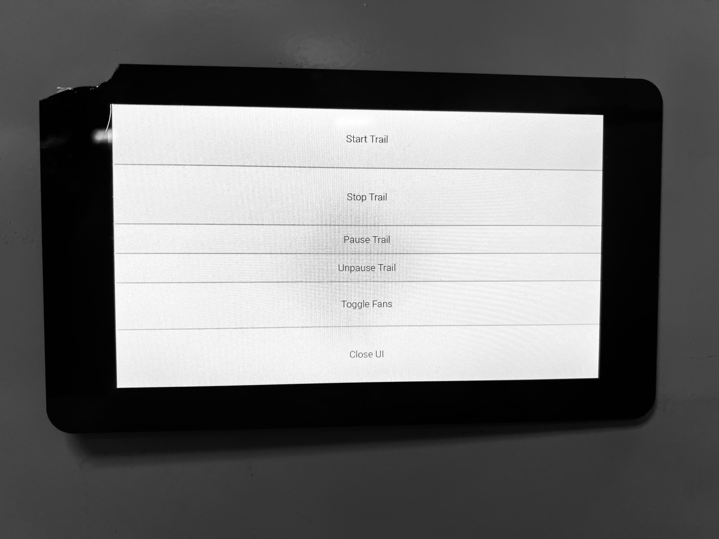
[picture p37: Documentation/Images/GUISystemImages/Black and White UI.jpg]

| Item | Testing Method |Expected Results | Actual Results | Was The Constraint Fulfilled |
|---|---|---|---|---|
|Menu Interaction to Desired State|The goal of this constraint was to ensure the User does not get confused or frustrated while navigating through the menu. To eliminate this the GUI was simplified to have all the menu options be presented to the user on one page. This ensures that the user does not have to go through multiple different windows to achieve the desired result. To test this all menu interactions will be interacted with and placed into a state diagram to display all the possible menu interactions and their functions.|Since I designed the GUI to be straightforward for ease of use I believe there will be no issue in the user being confused or frustrated with the number of interactions it takes to get to their desired result. |Since all the buttons on the GUI are only set to do a specific task all of the buttons achieve their task and then return to the main menu waiting for the next user interaction. All the menu interactions were plotted in the state diagram in the State Diagram header below.|Yes|
#### State Diagram
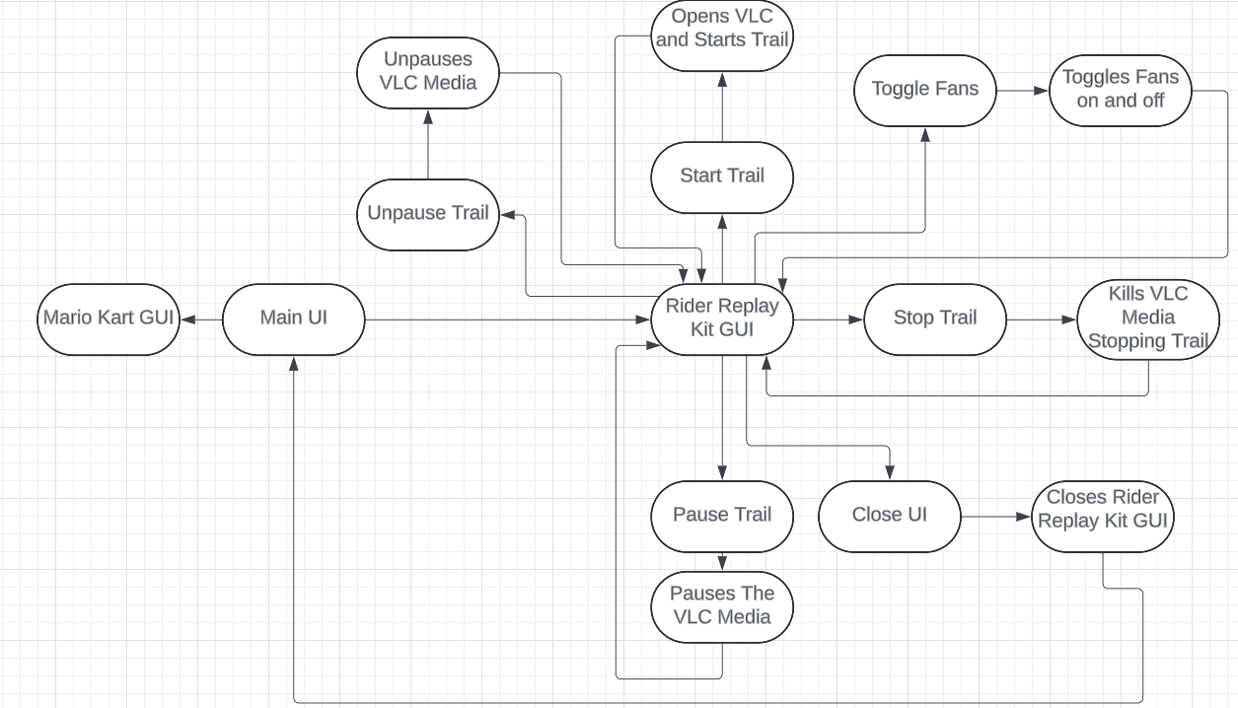
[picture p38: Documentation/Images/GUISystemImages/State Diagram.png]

| Item | Testing Method |Expected Results | Actual Results | Was The Constraint Fulfilled |
|---|---|---|---|---|
|Inputting User Weight/Difficulty selection|This was met by creating two additional pop-up windows that prompt the user to enter their weight and the difficulty they would like to be riding at. This will be tested by having the pop-up windows appear and then when the user selects their desired value it will print it out to the console to ensure it is being stored for later use in the work map.|I expect that the variable will be stored in the Python script under the desired variables and will be able to be seen in the console proving they have executed correctly|A combo box window appears and allows the user to select their weight from a drop-down menu and saves it to the user_weight variable. Similarly, on this box, the user is able to select from another drop-down menu their desired difficulty. Both of these values were tested multiple times with different values for weight and different difficulties and were in fact printed to the console.|Yes|

### Resistance Subsystem - Caleb Rozenboom

| Item | Testing Method | Expected Results | Actual Results | Interpretation |
|---|---|---|---|---|
| Connectivity | To send the force sensors (load cells) data to the Raspberry Pi, wireless communication is required. To accomplish this, BLE was used between the slave (Arduino on the pedals) and the master (Arduino connected to the pi). Communication from Arduino to Pi proved difficult, so an extra Arduino was used. The slave broadcasts its address, where then the master can find the address and connects to it. To test the reliability of the connection, ten connections were run and timed to ensure reliable connection from pedal data to raspberry pi. The graph of each run and its corresponding time to connect is pictured below. | The expectation of this experiment is the slave communicates data correctly to the master, ultimately sending data from the sensors to the raspberry pi in real time. | Connection was established, and the slave could send the data from the load cells over BLE to the master. | The results were as expected, connection could be established between the slave and master Arduino, and the time to connect is reasonable. Therefore, this constraint is fulfilled. | 

#### Connectivity Time Graph:


| Item | Testing Method | Expected Results | Actual Results | Interpretation |
|---|---|---|---|---|
| Work Map Access | To test if a work map can be uploaded and recreated using the linear actuator, a sample of work values was placed in a text file to then be extracted and converted into data for the linear actuator to move from. This is to prove that data from a trail can be collected and opened by the raspberry pi to then be recreated on the exercise bike. | The expected results of this experiment are to be able to open the work map, convert work values into actuator values, and move the actuator accordingly. | This experimentation resulted in readable data by the actuator, although did not stay within the resistance limitations for a rider to pedal (see actuator distance range constraint). The calculations from the signoff were used to convert work values into distance values for the actuator. The actuator moved in a scalable way from the work values. | The results were as expected, as readable data was sent to the actuator from a work map. Therefore, this constraint is fulfilled. |

#### Work Map Graph:


| Item | Testing Method | Expected Results | Actual Results | Interpretation |
|---|---|---|---|---|
| Actuator Distance Range | This is an inherited constraint from the past team. Since much of the testing on the actuator is built off the past team's work, this same constraint is kept in place to allow a rideable trail recreation (not allowing for resistance values too high or too low for the safety of the user). The past team put into place a range of 2-25 mm between the actuator magnet and the aluminum flywheel. To test if this constraint has been fulfilled, all data sent to the actuator retained the boundary data points in software. A ruler was then used to measure the distance during the run of test values to validate. | The expected result from this experiment is to keep the actuator distance between the magnet and the flywheel between 2-25 mm. | The testing proved successful, the distance between the magnet and the flywheel stayed in the designated range of 2-25 mm. A plot of the results is shown below. | The results were as expected, since the range of 2-25 mm could be set. However, this range is not wide enough to account for all the work values in the work map. As a result, this constraint is no longer necessary, and a new range likely needs to be established to provide enough range for a trail ride playback. Nevertheless, the actuator distance range can be set, therefore, this constraint is fulfilled. |

#### Actuator Distance Graph:


| Item | Testing Method | Expected Results | Actual Results | Interpretation |
|---|---|---|---|---|
| Sensor Force Range | The load cells that were used instead of the original force sensor set a maximum force value of 200 kg (440.925 lbs.). The minimum force value is still set as low as possible to provide maximum sensitivity. With load cells, the minimum force is not as much of a concern, as the output is linear to the force input. To test this constraint, the load cells were strapped to the pedal and were subject to high force (rider weighing 170 lbs.) during a ride under high resistance. | The expected results of this experiment are that the force exerted during a ride does not exceed the maximum force set by the load cells (440.925 lbs.). | The largest force value obtained from the ride on a single pedal was 174 lbs., as seen in the graph below. This is well within the maximum force range of 440.925 lbs., meaning the load cells are never compromised. | Since the largest force value obtained did not exceed the stated maximum force, this constraint is fulfilled. |

#### Force Sensor Graph:


| Item | Testing Method | Expected Results | Actual Results | Interpretation |
|---|---|---|---|---|
| Security | Another concern with the resistance system is the security of the load cell circuit housing enclosure strapped beneath each pedal that hold both the HX711 board, the Arduino Nano 33 BLE, and the voltage source (three double A batteries). To test the security, during the Sensor Force Range constraint experimentation, the security of the enclosure was also tested. | The expected result of this experiment is the load cell circuit housing does not fall off during a ride and not inhibit a user's experience. | The result from this experiment was that the enclosure was too top heavy, contributing to a greater inhibition of rideability. | The original design for the sensor circuit enclosure was designed with a different sensor in mind. Although the enclosure and straps still function as intended, the load cells require an extra layer of material (wood) below them with holes beneath each cell to ensure the middle of each cell can bend to send force data. The thickness needs to be greatly reduced to minimize weight on the top of the pedal. Although the straps stayed intact during the test, due to the inhibition of rideability, this is not sufficient to prove this constraint fulfilled. |

### Immersion Subsystem - Caleb Turney

| Item | Testing Method | Expected Results | Actual Results | Interpretation |
|---|---|---|---|---|
|Off Switch|To allow the user to turn off the fan output when riding, an off switch was implemented into the GUI of the device. This switch is a toggle that limits the output of the fans once pressed. Once the option is pressed, the send data variable that initially reads from the sensor is replaced with a 0 value so that the fans are not receiving new inputs from the bike. This remains implemented until the user presses the switch again and allows the fan to read from the sensor. This was tested by running the program and pressing the switch multiple times during the bike's functional period.|The expectation for this constraint is that when button on the GUI is pressed, the fans will no longer spin or react to the users input on the bike. Then once the button is pressed again input is accepted|At each point in time that the switch was pressed, the fans displayed that they were receiving a value of zero and no longer outputted. This switch follows the off button constraint that was set therefore this constraint is fulfilled.|The button worked as intended, and provided a very quick response when turning the fans on and off. So no only was the constraint met but it was efficient well functioning|
|Fan Mapping|The speed of a fan is directly proportional to the PWM duty cycle that the fan is driven with. To test this mapping constraint and ensure that the fans output was mapped to the scaled wind speed, the sensor data sent from the pi to the arduino had to be scaled. The calculated values from the signoff for speed were taken and a ratio was created between that speed and the PWM range of the fan. The 8-bit PWM range for the fan was 0-255 and the RPM range of the fan was 0-5800 . This means that for every 1 PWM there was an equivalent 22.75 RPM. The PWM was then found for each calculated RPM value in the signoff so that there was an accurate PWM value for each scaled speed value. A ratio was then found by taking each of the calculated PWM values and dividing them by the scaled speed value they were associated with. This resulted in a value of 12.3732523. This value was taken and implemented into the code so that every value that was read from the sensor would be multiplied by it.|The expectation for this constraint was that the arduino controlling the fans would be able to read the incoming value from the bike and then respond with a proper PWM value that would result in a fan speed that was indicative of wind speed. The arduino serial monitor should show the current values from the bike and the mapped values as well. |The accuracy of this was tested by having the arduino display the speed that was read from the bike sensor and also the scaled PWM value that the fan was being driven with. The values that were displayed on the arduino matched the values that the Raspberry pi displayed were being sent. Then through the scale factor that was implemented into the code, the final PWM duty cycle values that were displayed appropriately matched what was outlined in the signoff.|The values were properly mapped and matched the table of values that was calculated in the signoff. Although we did not have the means to directly measure the wind speed being outputted from the fan, the numerical data that we were receiving indicated success|
|Fan Control|The fan control constraint was tested by running both the bike code and the arduino fan code at the same time. If the speed of the fans changed when the sent value of the bike speed changed, it meant that the fans were being properly controlled and adapting to new inputs.|The expected result of this constraint was for the fans to increase in speed whenever the user increased their speed on the bike. We should not only be able to feel the change in speed of the fans but also here an audible change as well since the fans were loud.|Whenever the user increased or decreased the speed, a new value was sent to the fans which resulted in visible and audible change in speed. This shows that the fans are indeed adjustable therefore this constraint is fulfilled.|Due to the fans changing speeds whenever the user would change speeds, it was confirmed that there was at least some of level of control being exerted on the fans by the bike. And because the fans were not outputting at a constant speed at all times it showed that they could be controlled and not just have static values|
|Output Noise Level|An app on the phone was used to test the output noise level of the fan. The fan was run at different speeds while the phone was held approximately 4 feet away.|The expectation for this constraint was that no matter what speed the fans were outputting, they would stay within the appropriate decibel range.|The max decibels that were read was around 65-66 dBA. This was tested at multiple different speeds to give a wide range of different sound output levels. This falls slightly outside the range set in this constraint but is within an acceptable margin for safe testing. Due to how close this value is to the constraint set it will not be considered fulfilled.|Although the datasheet for the fans said that the max decibels that the fan would output was around 59 dB, it was found that there were other factors that could affect the noise level of the fans. Much to our surprise, setting different PWM frequencies on the fan can have an effect on the noise level that the fan outputs. More research and testing on this frequency may result in a value that allows the fans to fall within a more acceptable sound level range.|
|Power|To test the power draw of the fan, the fan was connected to both the wall wart power supply and an adjustable bench power supply in the lab. A multimeter was connected so that both the voltage and the current draw of the fan could be measured.|The expectation of this constraint was that the fan would always be provided enough power no matter what speed it was running at. Even at max power draw, there should not be any indication that power ssupplies output was being capped and providing insuficient power to the fan|When the fan was run at full power, the voltage reading was approximately 11.3 and the current draw was 1.67. The adjustable power supply was used to confirm that the readings were not the result of a lack of power from the chosen wall wart power supply. This shows that the fan only used around 18.871 Watts of power.|The wall wart is rated to supply 60 Watts of power therefore it was reasonably inferred that the 28.8 watts of power outlined in the constraint were achievable. However, due to the fans not drawing that much power it cannot be said with 100% certainty that this is true. This constraint is considered fulfilled.|

### Work Subsystem - Jayden Marcom

| Item | Testing Method | Expected Results | Actual Results | Interpretation |
|---|---|---|---|---|
|Recording elevation and distance| We tested this by using a known elevation and using google maps to measure distance in miles to three decimal places then using these values to compare to the measured on the subsystem. This same distance was measured using the bike and subsystem 5 times.|The expected result is that the measured value is exactly the same as the distance from the google maps|The measured values at worst were 0.00123 miles off of the measured distance.| This value is only one rotation of the wheel more than the intended value and was only recorded once during the 5 attempts. The elevation was at worst 0.3 meters off the measured value.|
|Work Calculation|he original proposed way to measure this was using CAD software, however the same measurement was later proposed to be measured using an apple watch and comparing it to the calculated. We used the apple watch app to calculate joules expended and compared it to the value determined by the subsystem|To do this team 5 had two individuals who both had relatively similar weights (150lbs and 155lbs) do multiple runs of the same recording using an apple watch. The main results for the users were from the range 32 Kilojoules with minimal pedaling to 51 kilojoules with maximum pedaling. With the average being 42.5 Kilojoules. When comparing this to the work value from the subsystem which was measured to be 47 Kilojoules. *See the graph below |The result from the subsystem should be comparable to the average of the work measured during the test with the apple watch.|This result provides a work calculation that is 4.5 Kilojoules greater than the average work from the actual trail. This result is comparable.|

#### Work(kJ):
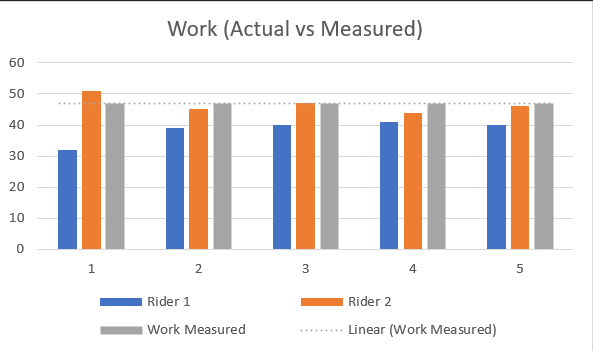
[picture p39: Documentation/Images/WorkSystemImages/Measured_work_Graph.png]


| Item | Testing Method | Expected Results | Actual Results | Interpretation |
|---|---|---|---|---|
|Distance between the box attached to the bike frame and the spoke(This constraint is less relevant due to the next constraint being more percise and applies to all bikes)|This was expected to be 20mm|This constraint was checked by measuring the depth of the 3d printed frame. |This value was .75 inch or 19.05mm.|The measured value was well within the expected |
|The magnetic sensor can be no more than 23.75 mm away from the magnet and it can be no closer than 12.7 mm.|This constraint was checked by attaching the box to the frame of the bike and measuring the distance to the magnet. The box was attached at the halfway point of the wheel’s radius. *The 3d printed holder was snapped before this test was able to be performed so the thickness of the holder is added during the calculations.|These values are expected to be lower than 23.75 mm for all bikes and greater than 12.7 mm.|See the graph following this section for datapoints. There is a single bike that was tested that provided a value below the 12.7mm|The bike that provided a value below 12.7mm was a BMX bike that did not contain any gears and had a tight set of back frame arms.|
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

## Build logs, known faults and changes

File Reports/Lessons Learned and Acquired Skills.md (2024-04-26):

# Lessons Learned

This document should have a section for each team member. Each engineer should respond to these:

- Reflect on the project, both technical and organizational. What went well? What didn’t go well? 
- What unanticipated problems occurred? 
- What would you do differently if you were to do it over again? 
- What “best practices” have you identified? 
- What words of wisdom would you pass on to future students?
- What new knowledge or skills did you acquire throughout capstone.

Create a subsection addressing each of the above questions in your section of the document. 

# Jayden Marcom
  For my subsystem most things went well the only thing that didn't go well is the accuracy of the pressure sensor. The pressure sensor is currently inaccurate by about 3 feet and I believe that could be further improved. Some unanticipated problems that occured is the idea of what should happen if there was a perfectly flat trail recording. Currently there is no set solution to the problem since it's purely hypothetical, but since the user on the bike and on the trail would just have to pedal the bike the back actuator shouldn't place any resistance on the back flywheel. If I were to go back and do it over again I would spend more time reviewing the previous teams work and understanding what exactly they were trying to do with specific systems. The best practice that I have identified are keeping backups of everything. You never know when you might need it. The words of wisdom I would like to relay is always be willing to help your teammates since later on they would be willing to help you. Some new knowledge that I aquired during capstone is teamwork, B field calculations, python coding, coding on an ubuntu interface, and many mathematical concepts. 

# Ben Ebel 
The creation of the GUI and implementation both went well and didn’t go well and was the main struggle for me. The GUI started out working but when it came time to implement the scaling code for the video it was tough to do. So tough in fact that I switched GUI libraries and ended up using multi threading to do so. However, in doing this it made the interaction with the GUI and the user very seamless. 

Dealing with infinite loops was the hardest part of my systems. It was eventually fixed with the use of the threading library in Python but this was a headache to deal with before discovering threading.

I would do better research on the previous team’s implementation. There were multiple times where our group assumed that the past group had actually got a system working but it then turned out that only half the system worked. So I would do more research in general.

I think the best practices are to research and try to find others who have done what you are trying to do or something similar to what you are trying to do.

I would suggest to them that they do more research on their topic before choosing. Always do more research than you think, whether that be into a topic you’re basing your system off or a topic other people are basing their system off because it could come to bite you.

I learned a lot about how to code in Python and interface with raspberry pis. I also learned a lot about how to function in a team dynamic. Additionally, I learned to always be prepared for the worst case scenario because almost nothing is going to work how you think it will and you will have to learn how to be on your feet.

# Jesse Brewster
  My subsystem was the audio subsystem, and overall the audio was successfully played back in accordance to the work done by the user on the exercise bike. So the basis of the experiment was completed. However what I hoped to accomplish was to divide the trail audio file into audio sections based upon commonly occurring frequencies such as a waterfall, and to loop these sections until the user progressed past them. This was not able to be accomplished due to the incompatibility of the machine learning software with the Raspberry Pi, more specifically the Python Libraries were not compatible. An unanticipated problem occurred whenever I had completed the audio code on my personal computer with the audio succesfully playing, but when I transferred the code to the Raspberry Pi the code had trouble working because it was originally designed to work on a Windows based system, not a Linux based system that was loaded onto the Raspberry Pi. 
  
  If I were to do this again, I would have done more testing with the Raspberry Pi itself to more fully understand how to make the Python code works and to fix any problems that arose. The best practice I learned was to always ask for help when needed and always be willing to help other group members when possible. This creates a better work environment and a willingness to accompish goals collaboratively. For the future members, ensure that you start your subsystems as soon as possible. The testing will take longer than expected, and make sure to document all codes and experiments so future members can understand the process behind everything. Also, taking on a third iteration of a project can be challenging because you have to review two other preious groups work and identify what worked well and what didn't, then use the devices they chose to buy instead of your own. A new skill I learned was how to program in Python, working with linux-based system, and how to process and divide audio files just through coding.

# Caleb Rozenboom
  For the Resistance Subsystem, quite a lot went well. The actuator moves, and the load cells read force and send via BLE to the other Arduino. The problems came with communicating with the other systems. More time needs to be spent in communicating with the other systems, since most time was spent getting the BLE set up. Another issue was getting the actuator to move, which also sucked up the majority of the time. Something helpful would be condensing the other two iterations into a more concise format, since so much documentation is involved, and it is hard to sift through what is useful and what is not. If I were to do this project again, I would spend more time on connectivity and communicating with the other systems, specifically testing the ability to move the work map based on change in work. My best practice for this project: ask questions. If you do not know the answer, look it up. If you cannot find what you are looking for, ask for help. There is no shame in not knowing anything. Specifically with this project, look through the documentation. If you cannot find it, look harder. My words of wisdom for other students is do your research! Especially while choosing your project/system. Before this project, I had no Arduino, raspberry pi, python, or BLE experience. I had to learn basically everything about my system. I am thankful for getting the chance to learn these skills and getting to apply them in a real project. 
  
# Utsav Singha

I was over the Video Subsystem, and overall the subsystem went well. Getting the original video to play through VLC Media Player was a smooth process and figuring out how Flowframes work also did not take much tinkering. However, getting the video to scale to the user's pedaling speed was an arduous process. Initially the previous team's code to determine speed did not work, however after we switched to using multiple threads to run all the systems individually, the integration was easy.

An unanticipated problem was the fact that initially VLC Media Player would not close out the video replay unless the video was completed, or it was taskkilled through the task manager. Another issue was that when the video was completed, the VLC Media Player would close out automatically This was later fixed by adding another more lines of code to force quit the replay if the user pleases, and to stay open until the user would close out of the video themselves.

Something I would do differently if I were to do the project over again is to research more on the different projects before picking the project to do for the year. Something that sounds cool, may not be the best project in execution, or may not have been left in the best state. I also would have done more experimentation and research with the RaspberryPi in the project to make sure that the proposals that were suggested were even feasable.

The best practice I learned is to ask for advice, whether that be from fellow students or group members, professors, or the internet. Asking for advice on how to run not only the system I was over, but also my teammate's systems, really helped out on making my subsystem work, and in finishing out the project.

As a word of advice to future students, I would suggest doing more research on the project as a whole. Learning on how not only your systems works, but how your teammate's system works will help greatly on getting the project done and working when it comes time to bringing everything together. Something that worked alone may not work when integrated with another system. 

Throughout the course of Capstone II, I learned how to problem solve and work within a team much better than I did before. I had to learn to improvise and research to get my system completed and consult with my teammates to certify that my system would work in tandem with the other systems to complete the Ride Replay Kit.

# Caleb Turney

I was responsible for the immersion subsystem. As this was my second tike taking the class I was able to apply some of the lessons learned that I had learned before to this semester. Some of the new lessons that I have learned are things like creating proper documentation for the work that I do. Going through the previous teams documentations helped me to realize the importance of it as it was challenging at times to find the necessary information I needed to progress my work. I have learned to more dilgently complete my work and help others out with their work as well. Above all, and the biggest lesson I have learned, is to complete my assigned team review evaluations.

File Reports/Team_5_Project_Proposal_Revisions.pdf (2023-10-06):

# Team 5 - Ride Replay Kit

Benjamin Ebel
Electrical and Computer
Engineering Department
Tennessee Technological University Cookeville, TN
baebel43@tntech.edu

Jayden Marcom
Electrical and Computer
Engineering Department
Tennessee Technological University Cookeville, TN
jtmarcom42@tntech.edu

Utsav Singha
Electrical and Computer
Engineering Department
Tennessee Technological University Cookeville, TN
usingha42@tntech.edu

Jesse Brewster
Electrical and Computer
Engineering Department
Tennessee Technological University Cookeville, TN
jibrewster42@tntech.edu

Caleb Rozenboom
Electrical and Computer
Engineering Department
Tennessee Technological University Cookeville, TN
cmrozenboo42@tntech.edu

Abstract – The purpose of this proposal is to introduce Team 5’s idea for the Fall 2023/Spring 2024 Capstone Project. The document begins with an overview of the identified problems, followed by a clear formulation of the issues at hand. Moreover, it dives into the necessary
specifications, | background | context, | and | constraints
relevant to the project’s scope. The proposal further outlines potential solutions and highlights criteria for assessing success, as well as potential obstacles. Additionally, a consideration of the broader ethical and societal impacts. Lastly, Team 5 provides an overview of the resources available and needed to complete the project, a timeline of due dates, and expectations of the project.

Keywords - Ride Replay Kit, exercise bike, mountain bike, variable resistance, visual and audio interpretation, feedback, work, Capstone Design, exercise, sensors, engineering, resistance, trail

I. INTRODUCTION

From biking The Great Mountain Divide to Cane Creek Park, imagine if you were able to transport yourself to these exotic destinations without having to leave the comfort of your home. Team 5 aims to allow users with limited time and or resources to experience these trails for themselves.
The Mario Kart Exercise Bike along with the Ride Replay Kit were designed by our predecessors to combine video games and exercise, as well as, give users the ability to go out onto a bike trail, film the course, and replay the course on the exercise bike. However, the kit has still not been tested successfully in the field.
The current problem Team 5 is encountering is that there is no way with the current system to accurately recreate the trail. The solution Team 5 has come up with is to completely implement the Ride Replay Kit with the following additions: the ability to replay trials recorded in the real world with accurate work exerted by the user, virtual recreation of the difficulty of the trail with scalability, visuals of the trail that will scale with the user’s pace, audio from the trail that will scale with the user’s pace, and a closed loop feedback system for the resistance. Team 5 proposes to capture the data from an actual bike trail in Cookeville and implement this.
The generalized goal of Team 5 is to continue to enhance the riding experience of its users and make the Ride Replay Kit appealing to a larger user base. Exercise bikes are still proven to strengthen cardiovascular, muscular, and respiratory health [1]. Continuing to enhance the experience for users in addition to expanding the use cases variety of the device should in turn bring in more users previously not interested in this product. This will make the project appeal to a wider variety of users who would like to go to these destinations but do not have the funds or the resources to do so.
This proposal entails Team 5’s plan to implement the enhancements to the project listed above. Team 5 will further explain the background of the project alongside the objectives, specifications and constraints,and standards adhered to by Team 5. This is followed by Team 5’s measures of success, unknowns and obstacles to be faced, and broader considerations. Lastly, Team 5 will showcase the components and budget, the skills of Team 5, a timeline, and any outside references needed for this document.

II. FORMULATING THE PROBLEM

A. Background
The first iteration of this project set out to integrate physical exercise in tandem with playing Mario Kart, this was in order to promote health and fitness to a new demographic. The overarching goal was to be able to interact and play through Mario Kart tracks on a Nintendo switch utilizing an exercise bike. This first iteration achieved its overarching goal but was improved upon by the second revision. The second iteration of the Mario Kart Bike sought out to improve the dynamic resistance system, and to add the Ride Replay system. The second iteration added an actuator with two magnets and an aluminum flywheel attached to the back wheel of the bike to make the resistance system more variable and safer for the user. The team designed a kit from scratch to attach to a bike that can record data from an outdoor ride to recreate the corresponding ride on the exercise bike. Looking at the previous iteration of the bike, the resistance subsystem is an open loop system which makes the system more static. Team 5 intends to make the resistance system more variable and dynamic. Team 5 will seek to implement a work calculation subsystem to provide a more realistic resistance to the user, keeping the total work done on the exercise bike consistent with the trail. The ride replay system did work properly but was damaged during testing and needs to be repaired and officially implemented.
B. Objective

The objective of Team 5 is to accurately recreate the difficulty and ambiance of a bike trail on the exercise bike. Team 5 will achieve this objective by improving the Ride Replay Kit produced by Team 4. The improvements to be made to the Ride Replay Kit are to help enhance the immersion of the user, and to make the user’s ride as close to the real trail as possible. The new Ride Replay Kit will have the ability to measure the work done by the user on the trail in order match this to the work done on the exercise bike. The resistance system currently on the exercise bike will be modified to be a closed-loop feedback system to respond to the user’s pace on the trail. The audio and visual data will be recorded from the trail to give the user auditory and visual immersion into the trail. Finally, improvements to the user interface will allow the user to input weight, select from different difficulties and trails, see the work they have done, and inform the rider of the time spent on the exercise bike. These additions to the Ride Replay Kit should provide the user with a safe, enjoyable, and accurate experience of how the bike trail being replayed feels.

C. Specifications and Constraints

The Ride Replay Kit will include all the necessary hardware to measure and accurately recreate the trail to provide the user with an immersive experience. These are achieved by the work measurement system, closed-loop feedback resistance system, audio processing system, visual processing system, user interface.
1) Work System: The Ride Replay Kit will record the elevation, distance, and time to calculate the work done on the bike trail.
2) Resistance System: The resistance of the system (or the distance of the actuator) will adjust according to the rider’s pace in order to maintain the correct work done on the trail.
3) User Interface: A user interface will allow the user to interact with the ride replay system in the following ways: input of the user’s weight, selection of the trails, selection of the difficulty of the trails, display the work done by the user, and notify the user of the time they have spent on the bike to avoid overexertion.
4) Audio System: A microphone will record the audio from the trail in order to replay it for the user to enhance the immersive experience of the bike. The audio playback will not exceed 80 dB to prevent hearing loss or damage.
5) Visual System: A camera will record the video from the trail and replay it at a quality resolution with a consistent frame rate. The video is set at these specifications in order to not cause the user to experience motion sickness while riding the exercise bike.
6) Repairs to Previous System: The Ride Replay Kit was damaged in testing by the last capstone group and needs to be repaired in order to be used. The exercise bike handle bar gears also need to replace since the previous iteration has had issues with them.
D. Standards
1) Mechanics:
- 1926.300b.2 - OSHA Standard for Guarding from Rotating or Moving Parts of Equipment
- ASTM F1250-13 Standard Specification for Stationary Upright and Recumbent Exercise Bicycles and Upper Body Ergometers
2) Electronics:
- 1926.404b OSHA Standard for Wiring Design and Protection
- 1910.137 OSHA Standard for Electrical Protective Equipment
- IEC/IEEE 62209-1528:2020 human exposure to radio frequency fields from hand-held devices.
- Our device will comply with all applicable regulations set within Title 47 Part 15 of the Code of Federal Regulations.
– 15.1 states that any radiator (that which emits radio energy), whether or not intentional, must be licensed. – Prohibits intentional damped wave transmissions such as spark-gap transmitters.

III. SOLUTIONS

A. Measures of Success

This section will provide a overview of the measures of success for each subsystem, and the means to test for validation. This is to provide a good grasp on the completeness of the project as a whole, as well as different steps to take around obstacles to ensure a complete project. Team 5 will test each subsystem in the following ways:

1) Work System: In order to validate the success of the Work system Team 5 will compare the work from the trail to the work done on the recreation of the trail on the exercise bike. To do this Team 5 will use the Apple Watch workout app to measure the work done on the trail and use the same app to remeasure the work on the exercise bike. This experiment will be repeated various times using the same trail but with different members of the team of varying weights. The work system will be declared as successful when the work done on the trail matches the work done on the exercise bike.
2) Resistance: In order to validate the success of the Resistance system Team 5 will compare the work from the optimal playback of the trail with different variations of force input from the user. To do this Team 5 will test the bike at varying levels of force making sure that the total work stays comparable to the actual work done over the trail. The resistance system will be declared as successful when the resistance on the exercise bike (or the distance of the actuator) matches the calculated resistance (or distance) to provide the correct work of the specific position on the trail.
3) User Interface: In order to validate the success of the user interface, Team 5 will record interactions between the user and the user interface. To do this Team 5 will use the Technique app to record the interaction at a high FPS in order to get an exact moment of contact and response. This experiment will be repeated with differing speeds and intensity of presses. The user interface will be declared as successful when the measured latency is within the acceptable range.
4) Visual System: In order to measure the success of the visual system Team 5 will compare the recording to the actual visuals on the trail. To do this the test rider recording the trail will have to verify that the surroundings seen on the trail match the video captured of the trail. This experiment will be repeated using multiple recordings of the same trail and comparing them with the physical trail. The visual system will be declared as successful when the desired visual play back matches the captured data from the trail.
5) Audio System: In order to validate the success of the audio system Team 5 will select high and low sounds from the recording and compare them to the outputs of the same sounds on the speaker. To do this Team 5 will compare the audio wavelength of specific sounds recorded to the output wavelengths of the same specific sounds through the speakers. This experiment will be repeated using varying wavelengths of sounds ensuring that the output wavelength matches the input. The audio system will be declared as successful when the audio wavelengths captured from the microphone matches the wavelengths from the speakers on the exercise bike.
B. Unknowns, Obstacles, and Safety Concerns
Team 5 may experience a number of obstacles. One of these may be the sensors on the Ride Replay Kit, these were implemented by the previous capstone group before the Ride Replay Kit was damaged which means they may need to be replaced. Team 5 will test Ride Replay Kit to ensure complete functionality before recording a trail to be replayed.

The current camera within the Ride Replay kit has a lessthan-desirable frame rate for a smooth replay experience. When the user is replaying a bike trail, they could potentially slow down their pedaling, which would then slow down the frame rate of the playback video. When slowing down the frame rate a slow frame speed could cause the user to experience choppy visual playback, taking away from the immersion. Team 5 will seek to solve this issue using the testing procedure declared under the ”Measures of Success” section.
To avoid harming the user’s hearing, the audio output should not be above 80 decibels to comply with the regulations set by OSHA standards [2]. We will ensure compliance by taking the maximum input from the microphone on the ride replay kit, and the maximum output from the speakers on the exercise bike, and calculating the maximum possible dB output. Careful testing will be done as mentioned in ”Measures of Success” to keep audio levels at a safe value.
Another potential obstacle Team 5 could experience is an unstable or shaky camera when recording trails. This would give an unusable recording for the exercise bike to replay. This can be mitigated by ensuring the camera is mounted firmly and shock absorption devices are correctly implemented.
C. Broader Considerations
- The Ride Replay Kit has minimal ethical concerns beyond reliability of the project and safety of the user. The main concern comes from overexertion of the user during a trail replay. To minimize this concern Team 5 implemented the notification to remind the user of the recommended amount time to spend exercising to prevent over exertion [3].
- The Ride Replay Kit would allow for access to a variety of trails. This would attract a new group of riders who, before seeing the trail replays, might not have been interested in using an exercise bike. This would also make a huge impact on existing mountain bikers by providing a new way to experience the trails without having to leave home.
- The Ride Replay Kit would impact environmental awareness of different locations and places where most people wouldn’t normally visit. This could include historical landmarks, national parks, or well-known urban areas. This could also cause users to take greater interest in the environment and potentially bring attention to issues affecting these trails.
- The Ride Replay Kit promotes many positive impacts on mental health. Exercise is known to benefit mental health and general well-being. It reduces insulin resistance, inflammation, and stress hormones, leading to more healthy and strong brain cells [4].
- The Ride Replay Kit will provide accessibility to users who are unable to visit these bike trails due to varying reasons, such as those with solar urticaria, agoraphobia, or severe allergies.

IV. RESOURCES AND REQUIREMENTS FOR IMPLEMENTATION

A. Budget and Components

TABLE I
THE BILL OF MATERIALS

Bill of Materials
Material | Cost (USD) | Example
Force Sensor (4x) | $120 | https://tinyurl.com/5n8f4cv2
Microphone | $40 | https://tinyurl.com/2c6mxmum
Speakers | $40 | https://tinyurl.com/5c2j39vm
Camera | $425 | https://tinyurl.com/2967surp
Bluetooth Module (2x) | $30 | https://tinyurl.com/2uyhm89x
Unforeseen Costs | $105
Total Cost | $760

In order to accurately measure work Team 5 requires force sensors that will be mounted on the pedals of the exercise bike to ensure work measured matches work calculated. The Bluetooth modules are needed to transmit the force data from the force sensors to the Arduino for work calculation. This also removes the need to hard-wire the force sensors to the pedals. To simulate audio from the recorded trails, Team 5 needs a microphone to capture the sounds of the environment. Speakers are required to replay these audio files from the recorded trails to create an immersive experience for the user. Team 5 also aims to create an immersive visual experience for the user and will therefore require a camera with a high refresh rate and resolution. A high resolution and refresh rate camera may be provided for recording bike trails, which could possibly save the budget $425. Team 5 added a 15 percent padding to the budget to account for any unforeseen cost and damages or malfunctions to components.

B. Team Members

The following list is meant to reflect the key proficiencies of each team member.

1) Ben Ebel:
- Embedded Systems
- C++/C♯/C
- Circuit Design/Analysis
- SQL
- Excel
- Microsoft Access Database
- Digital System Design
2) Caleb Rozenboom:
- Altium PCB Design and Circuit Schematic Creation
- Soldering
- Circuit Design/Testing/Analysis
- AutoCAD
- Electromagnetic Fields
- PLC installation and troubleshooting
- MS Excel
- LTSpice Simulation
- Project Management
3) Jayden Marcom:
- AutoCAD
- Print Reading
- C++
- Power Automate
- Simulink
- Excel
- Circuit Design
- Power Systems
- Arduino
- Solidworks
- Soldering
4) Jesse Brewster:
- PCB Design and Circuit Schematic Creation within Altium.
- Soldering and Micro-soldering
- AutoCAD
- MS Excel
- PLC design and programming
- Arduino
- 3D Modeling within SolidWorks/Inventor
5) Utsav Singha:
- Experience in AI coding and implementation
- High level competency with Microsoft Suite of Software
- Electromagnetic Fields
- Experience in Spice circuit simulation
- Soldering
- Project management
- Technical Writing
- Experience in MySQL
- Circuit Design/Testing/Analysis
C. Timeline
The timeline shown below represents an accurate chronological order for progress checkpoints throughout the project.
1) September:
- Project Proposal Due
2) October:
- Conceptual Design Due
- Project Proposal Revision due
- Detail Design Checkpoint 1
- Midterm Progress Presentation
3) November:
- Detail Design Checkpoint 2
- GitHub Customization and Update
4) December:
- Final Presentation

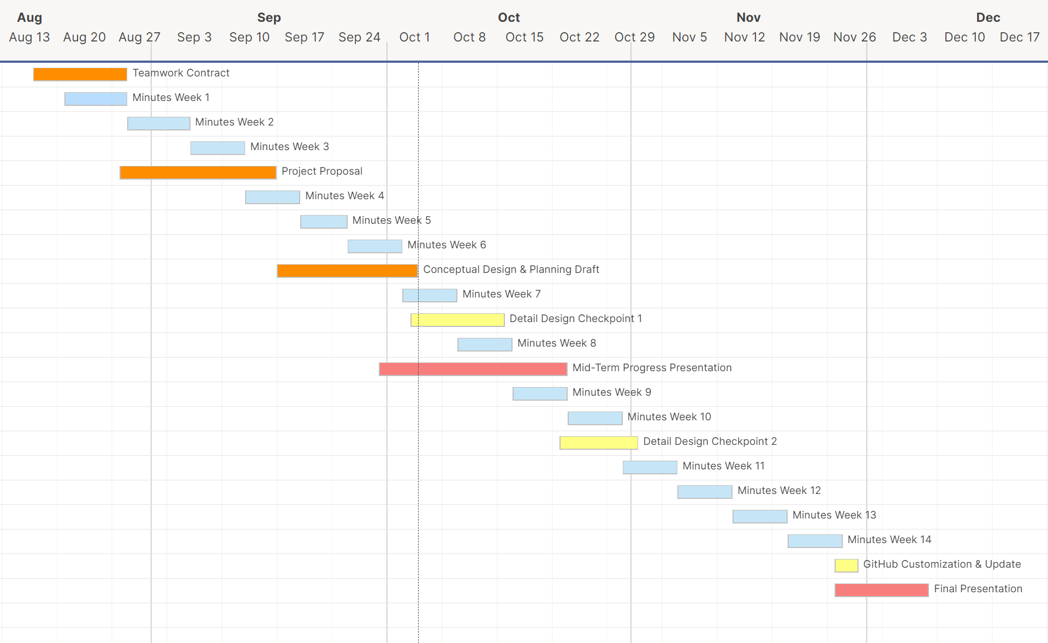
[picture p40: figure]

Fig. 1. Gantt chart timeline

REFERENCES

[1] M. Chavarrias, J. Carlos-Vivas, D. Collado-Mateo, and J. Perez-G ´ omez, ´ “Health benefits of indoor cycling: A systematic review,” Available at https://www.ncbi.nlm.nih.gov/pmc/articles/PMC6722762/ (2019).
[2] “Occupational safety and health administration,” Available at https://www.osha.gov/noise.
[3] K. Jeffery and S. Jennifer, Overtraining syndrome: a practical guide. Sports Health, 2012.
[4] A. Sharma, V. Madaan, and F. D. Petty, “Exercise for mental health,” Available at https://doi.org/10.4088/pcc.v08n0208a (2005).

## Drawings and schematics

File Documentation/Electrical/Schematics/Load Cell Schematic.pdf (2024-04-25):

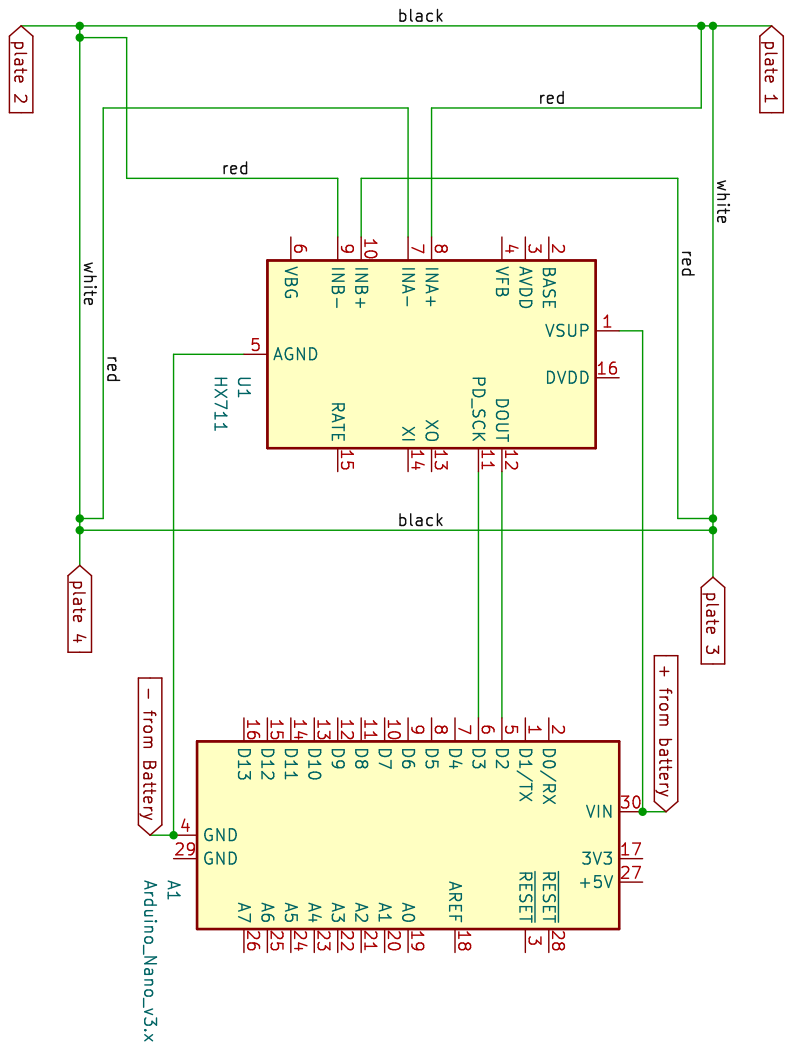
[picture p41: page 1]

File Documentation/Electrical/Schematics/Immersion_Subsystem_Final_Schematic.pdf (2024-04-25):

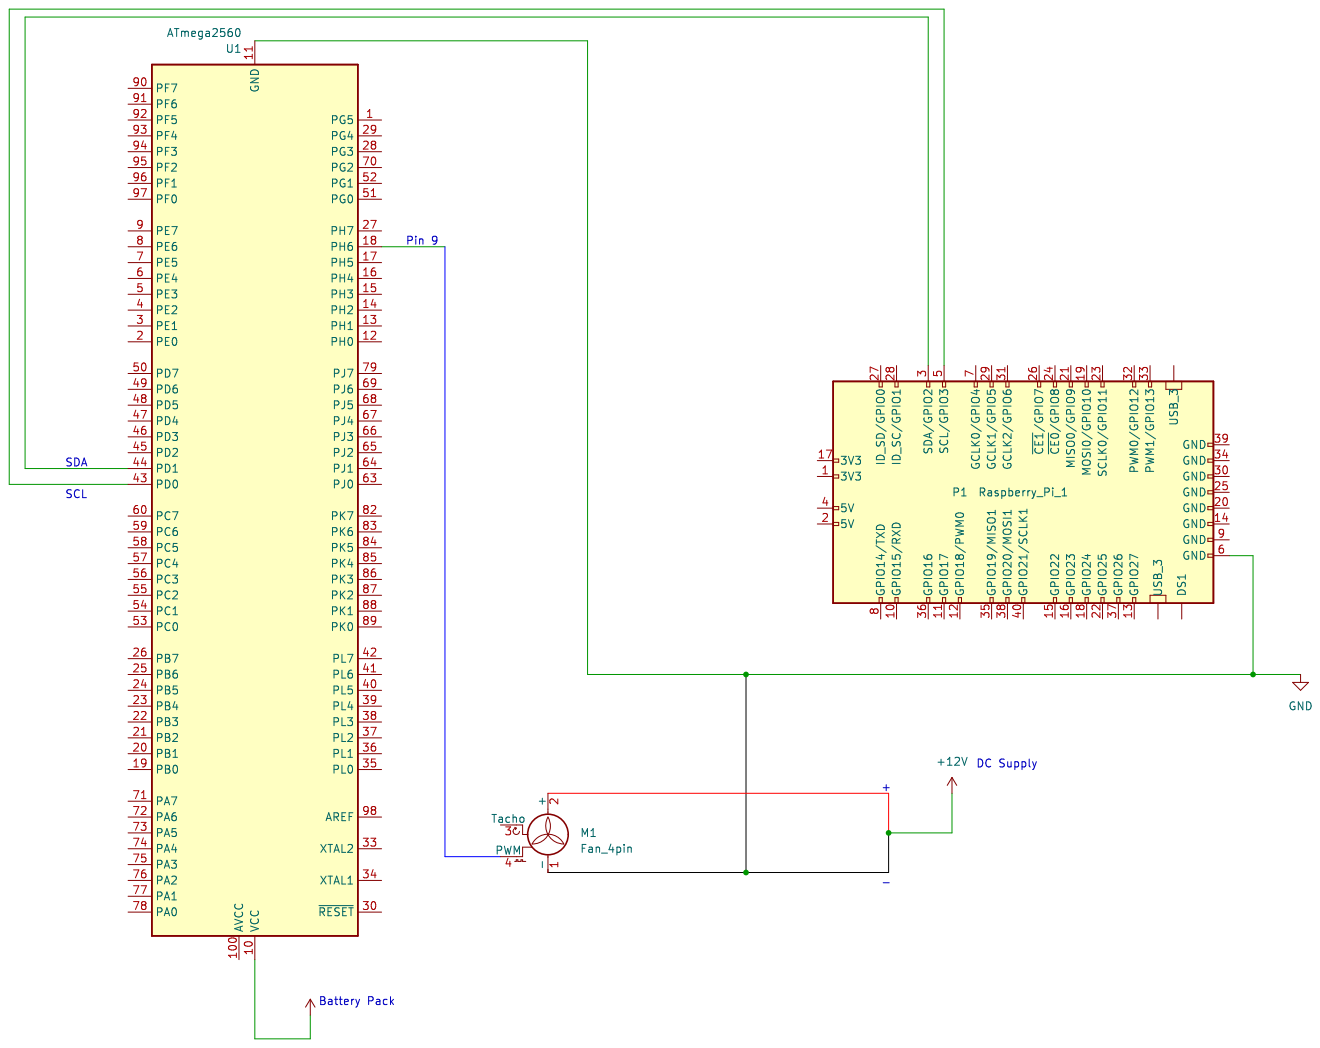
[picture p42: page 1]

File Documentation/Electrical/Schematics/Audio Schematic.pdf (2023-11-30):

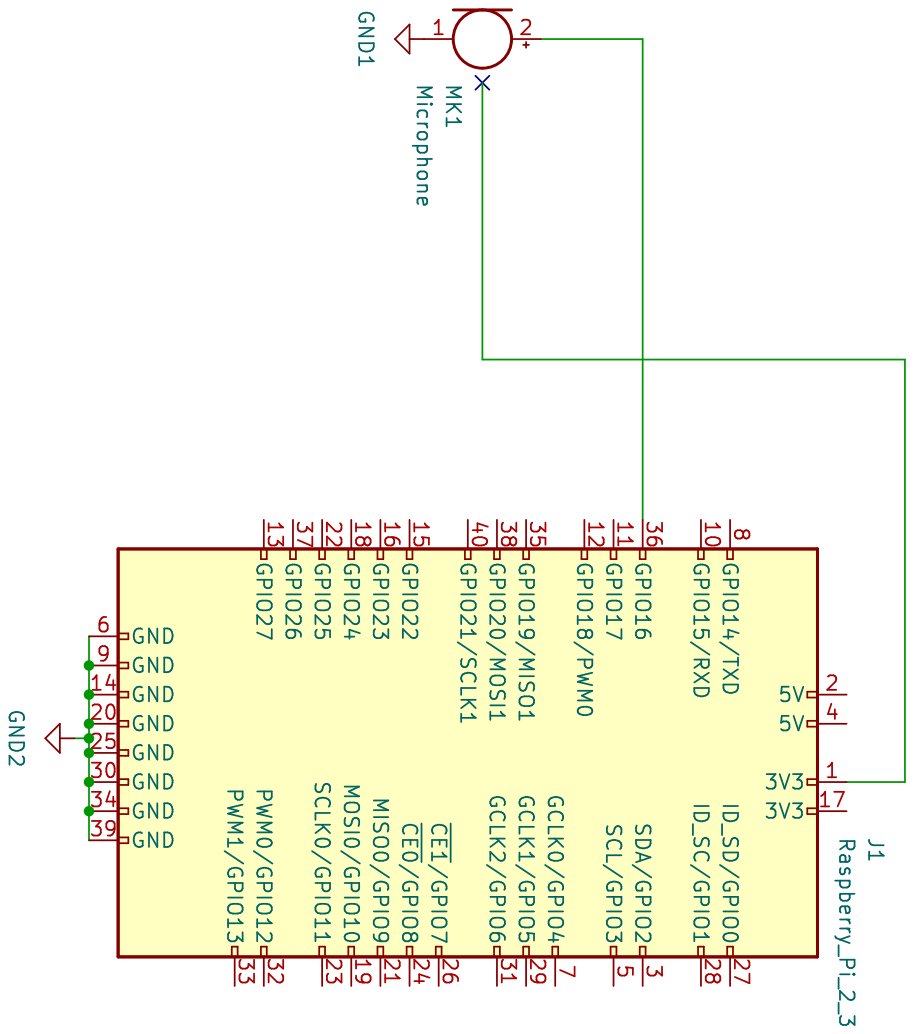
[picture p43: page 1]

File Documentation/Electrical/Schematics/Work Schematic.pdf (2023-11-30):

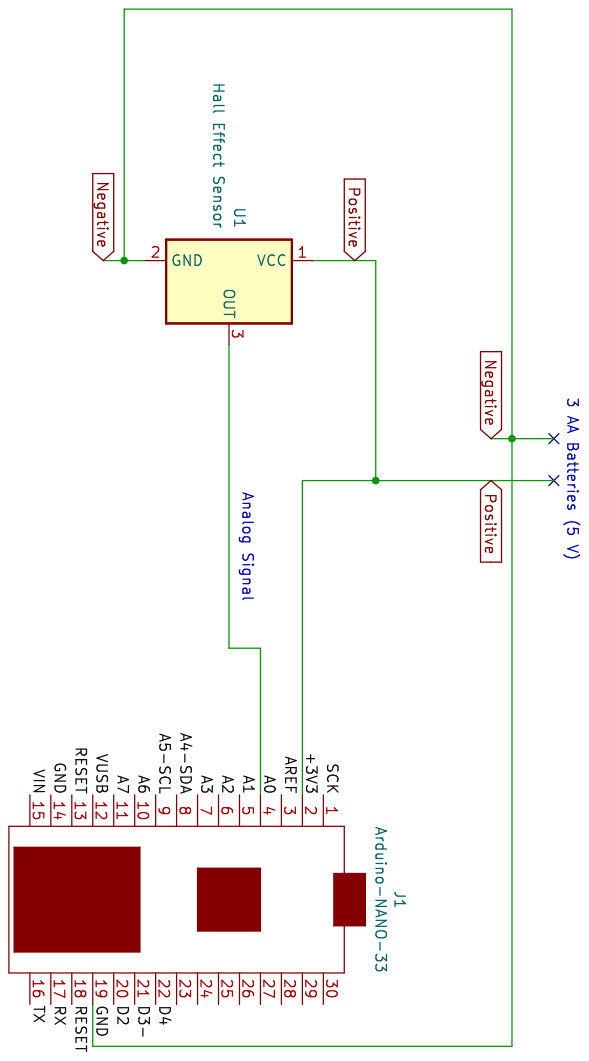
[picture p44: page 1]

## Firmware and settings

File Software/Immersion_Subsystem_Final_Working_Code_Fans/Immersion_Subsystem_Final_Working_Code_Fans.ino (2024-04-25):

#include <Wire.h>
#define SLAVE_ADDRESS 0x08
#define FAN_PIN 9  // PWM pin connected to the fan control wire
#define PWM_MAX 255  // Maximum PWM value (255 for 8-bit PWM)
int w = 0;
byte data_received = 0;
void setup() 
{
  Serial.begin(9600); //Initialize the Serial Monitor

  pinMode(FAN_PIN, OUTPUT); // Initialize PWM pin for fan control

// Set PWM frequency for Pin 9 (25 Khz)

// Set Timer/Counter2 to Fast PWM mode with non-inverted output
  TCCR2A = (1 << WGM21) | (1 << WGM20) | (1 << COM2A1);
  
  // Set prescaler to 64
  TCCR2B = (1 << CS22);

  Wire.begin(SLAVE_ADDRESS); //Setup For I2C Wiring with Rpi
  Wire.onReceive(receiveData);
  Wire.onRequest(sendData);
  
}
void loop() { 

int w = data_received; // Initialize variable for received Rpi data

Serial.println("Current Speed (MPH): "); //Prints out speed read from bike
Serial.println(w);
w = w * 12.3732523; // PWM to RPM Conversion Value
Serial.println("PWM Duty Cycle Value: "); //Prints converted PWM duty cycle value
Serial.println(w);
delay(300);


}

void receiveData(int bytecount) // Function for receiving I2C data from Rpi
{
  for (int i = 0; i < bytecount; i++) {
    data_received = Wire.read(); // Setting the variable to hold the data read from wire
       
  }
  int w = data_received;
   w = w * 12.3732523; // Value Calculated to scale speed values to appropriate PWM values
   if (255>=w>0) { // Loop for when PWM value is within appropriate limits

  analogWrite(FAN_PIN, w); // Writes the PWM duty cycle value to the pin to drive the fan 
  delay(20);
}
}
void sendData()
{
  Wire.write(data_received); // Sends received value back to Rpi
}

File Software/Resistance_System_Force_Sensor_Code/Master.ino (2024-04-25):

#include <ArduinoBLE.h>

struct DeviceInfo {
  String address;
  String uuid;
};

// Define an array of devices you want to interact with
DeviceInfo devices[] = {
  {"84:cc:a8:77:9f:1a", "3672"} // NANO 33 IOT for
};
int currentDeviceIndex = 0; // Index of the current device being processed

void setup() {
  Serial.begin(9600);
  while (!Serial);


  if (!BLE.begin()) {
    Serial.println("Failed");
    while (1);
  }    
  BLE.setLocalName("Master");
  Serial.println("Bluetooth Low Energy Central scan");
  BLE.scanForAddress("84:cc:a8:77:9f:1a"); // Start scanning without specifying an address
}

void loop() {
  // Check if we've gone through all devices
  if (currentDeviceIndex >= (sizeof(devices) / sizeof(devices[0]))) {
    Serial.println("Processed all devices. Restarting...");
    currentDeviceIndex = 0; // Optionally restart or halt the program
    //return; // Uncomment to stop after processing all devices
  }

  BLEDevice peripheral = BLE.available();

  if (peripheral) {
    // Get the current target device info
    DeviceInfo& targetDevice = devices[currentDeviceIndex];

    // Check if the found peripheral matches the target address
    if(peripheral.address() == targetDevice.address) {
      Serial.println("Discovered a peripheral");
      Serial.println("-----------------------");
      Serial.print("Address: ");
      Serial.println(peripheral.address());

      Serial.print("Local Name: ");
      Serial.println(peripheral.localName());

      Serial.print("UUID: ");
      Serial.print(peripheral.advertisedServiceUuid());
      Serial.println();

      BLE.stopScan();

      // Assuming explorerPeripheral function is adapted to use DeviceInfo
      explorerPeripheral(peripheral, targetDevice.uuid);

      // Move to the next device
      currentDeviceIndex++;
      BLE.scan(); // Restart scanning for the next device
    }
  }
}

void explorerPeripheral(BLEDevice peripheral, String uuic) {
  // connect to the peripheral
  Serial.println("Connecting ...");

  if (peripheral.connect()) {
    Serial.println("Connected");
  } else {
    Serial.println("Failed to connect!");
    return;
  }

  // discover peripheral attributes
  Serial.println("Discovering attributes ...");
  if (peripheral.discoverAttributes()) {
    Serial.println("Attributes discovered");
  } else {
    Serial.println("Attribute discovery failed!");
    peripheral.disconnect();
    return;
  }

  // loop the services of the peripheral and explore each
  for (int i = 0; i < peripheral.serviceCount(); i++) {
    BLEService service = peripheral.service(i);
    exploreService(service);
  }

  Serial.println();
}

void exploreService(BLEService service) {
  // Filter for services with UUIDs 180D and 180C
  const char* serviceUUID = service.uuid();
  if(strcmp(serviceUUID, "3672") == 0){
    Serial.print("Service ");
    Serial.println(serviceUUID);

    // Loop the characteristics of the service and explore each
    for (int i = 0; i < service.characteristicCount(); i++) {
      BLECharacteristic characteristic = service.characteristic(i);
      // Filter for characteristic with UUID 2A57
      if(strcmp(characteristic.uuid(), "4783") == 0){
        exploreCharacteristic(characteristic);
      }
    }
  }
}

void exploreCharacteristic(BLECharacteristic characteristic) {
  // Print the UUID and properties of the characteristic
  Serial.print("\tCharacteristic ");
  Serial.print(characteristic.uuid());

  // Check if the characteristic is readable
  if (characteristic.canRead()) {
    while(true) { // Continuously read the characteristic value
      // Read the characteristic value
      characteristic.read();

      if (characteristic.valueLength() > 0) {
        // Print out the value of the characteristic
        Serial.print(" value 0x");
        printData(characteristic.value(), characteristic.valueLength());
        Serial.println();
      }
      delay(200); // Add delay to prevent flooding
    }
  }
  Serial.println();
}

void printData(const unsigned char data[], int length) {
  for (int i = 0; i < length; i++) {
    unsigned char b = data[i];

    if (b < 16) {
      Serial.print("0");
    }

    Serial.print(b, HEX);

  }
}

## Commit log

2023-10-31 WorkSystenSignoffAttempt2.md
    Fixed
    - Clarify Distance Constraints for spoke and frame
    - Set a minimum gap between sensor and magnet
    - Explain constraint on wheels size
    - Add minimum sensing speed
    - Change to splash resistant instead of water proof
    - Change sending protocol to a more energy efficient type
    - Remove Arduino Uno
2023-10-31 Work Subsystem Signoff Attempt 2
    Apologies I thought I messed up the way to commit changes but it turns out I did not. I cannot find a way to undo the commit so I am reuploading the file with the same comments.
    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
2023-11-01 Requesting Signoff for revision 3
    Replaced the Zigbee with a BLE arduino
    and found a lithium-ion battery capable of supplying appropriate voltage for the set time constraint
2023-11-02 Update Resistance Subsystem.md
2023-11-02 Requesting Signoff for Revision 4
    I believe we have addressed the Nyquist Rate
    Fixed the system to work with 3 AA batteries in series with explanation of the decay pattern
    Fixed Schematics and CAD files to accommodate new components
    Updated BOM, we left the sealants but will not put them on the purchase order
2023-11-06 Resistance Subsystem.md
    Revision 1
2023-11-08 Requesting signoff for revision 7
    Added math for slowest external read frequency on the Arduino nano
2023-11-08 Update WorkSysten(1).md
    Changed the arduino calculations from 20kHz to the correct 16 ksps
2023-11-16 Requesting Signoff for Revision of the GUI subsystem
    I have changed the system to take in the user interaction as a high-priority interrupt. I believe that you still wanted me to mention the 300 ms delay but if you feel this is not necessary anymore, s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
2023-11-27 Resistance System Images
    Housing on Bike
2023-11-27 Resistance Subsystem.md
    Rev 2
2023-11-30 Work System SolidWorks Files
    [WorkSystemDesignBoxV4.SLDPRT, WorkSystemLidV4.SLDPRT]
2023-11-30 Added Work System Schematics Folder
    [Magnet_Mount.SLDPRT, WorkSystemDesignBoxV4.SLDPRT, WorkSystemLidV4.SLDPRT]
2023-11-30 Work System 3D models
    [Magnet_Mount.SLDPRT, WorkSystemDesignBoxV4.SLDPRT, WorkSystemLidV4.SLDPRT]
2023-11-30 Resistance System Images
2023-11-30 Added Work System Schematic
    [WorkSystem.kicad_sch]
2023-11-30 Resistance Subsystem.md
    WIP
2023-11-30 added 3d models for work system
    [Magnet_Mount.STL, WorkSystemDesignBoxV4.STL, WorkSystemLidV4.STL]
2023-11-30 Update Audio.md
    Update To CAD Schematics
2023-11-30 Rename Resistance.pdf to Resistance Schematic.pdf
2023-11-30 Rename Audio.pdf to Audio Schematic.pdf
2023-11-30 Update and rename Resistance System Schematic.kicad_sch to ResistanceSchematic.kicad_sch
    [ResistanceSchematic.kicad_sch]
2023-11-30 Update and rename Audio.kicad_sch to AudioSchematic.kicad_sch
    [AudioSchematic.kicad_sch]
2023-11-30 Update and rename Work.kicad_sch to WorkSchematic.kicad_sch
    [WorkSchematic.kicad_sch]
2023-12-01 AudioAndVideoSystem 3D models
    [Camera and Mic mount - Gopro_6dz2-1.STL, Camera and Mic mount - Holder-1.STL, Camera and Mic mount - Whole Part.STL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]
2023-12-01 Resistance Subsystem.md
    Updated Revision
2024-01-31 Resistance Subsystem.md
2024-01-31 Resistance Subsystem Signoff.md
2024-02-07 Requesting Signoff for Audio Subsystem.md
    * Changed the cloud based service to Google Drive.
    * Got rid of speaker amplifier because it was unnecessary and decided to use computer speakers with a built in amp to reduce cost.
    * Explained how all libraries work within Python to process the audio and send it to the cloud.
    * Updated bill of materials
2024-02-10 Requesting Signoff of Audio Subsystem
    * Added Two Schematics:
    * Schematic for the microphone with all sensors included in
    * Schematic for the speakers including all devices as well
    Note: There are two Raspberry Pi's for this Subsystem. One is responsible for the recording of audio through the microphone. The other one is responsible for the playback of the audio through speaker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
2024-02-13 Requesting Sign Off of Audio Subsystem.md
    * Addressed the previous issues of speaker output.
    * Updated the schematics to show correct wiring of speakers and the new USB microphone we chose.
    * Also added CAD diagrams of Speaker cones and the Speaker Mounting system
2024-02-26 Update and rename Resistance Subsystem.md to Documentation/Signoffs/Resistance Subsystem.md
2024-04-11 Experimental Analysis Team 5.md
    Added resistance system
2024-04-16 Experimental Analysis Team 5.md
    update resistance system
2024-04-18 Experimental Analysis Team 5.md
    Update Resistance System Actuator distance constraint
2024-04-25 Add files via upload
    Adding Immersion Schematic PDF
2024-04-25 Add files via upload
    Adding KICAD schematic for immersion
    [Final_Immersion_Schematic.kicad_sch]
2024-04-25 Create Actuator Control for Resistance System
2024-04-25 Create FlowFrames
2024-04-25 Create FlowFrames_Install
2024-04-25 Update FlowFrames_Install
